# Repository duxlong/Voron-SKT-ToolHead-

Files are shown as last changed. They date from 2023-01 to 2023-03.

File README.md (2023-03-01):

# Voron SKT Toolhead
Mod for Voron with umbilical 
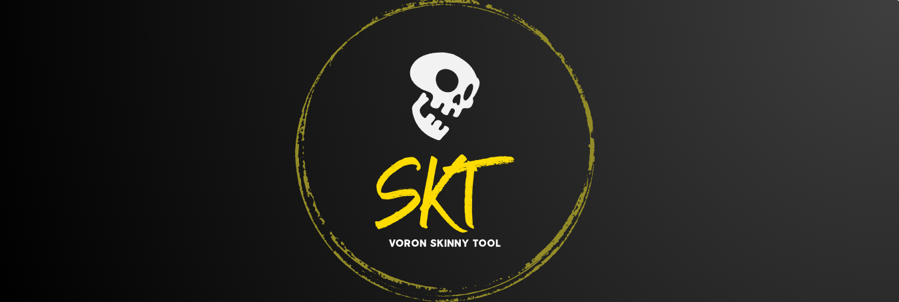
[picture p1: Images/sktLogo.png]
<br/>
<br/>
SKT stands for "Skinny Tool" :)<br/>
Some things are inspired by EVA 2, thanks guys.<br/>
This toolhead is designed to be as light as possible. It will not be compatible with all extruders and all hotends or even with all types of toolboards due to its design and specificity.<br/>
STK toolhead allow the installation of SHT42/EBB42 toolboards only.><br/>
If you want to run fast, just try it.<br/><br/>
There will be a CPAP cooling system as soon as possible (and will be compatible with Trident as well)<br/>

# Voron SKT Toolhead - Voron Tap Edition (for 2.4 and Trident)
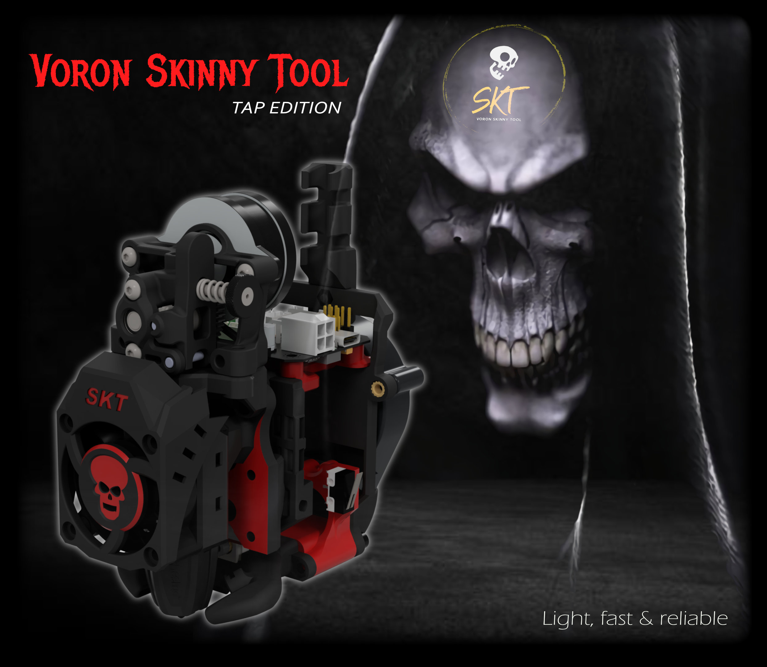
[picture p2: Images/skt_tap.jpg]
<br/>

# Voron SKT Toolhead - Klicky Edition (for 2.4, no Trident)
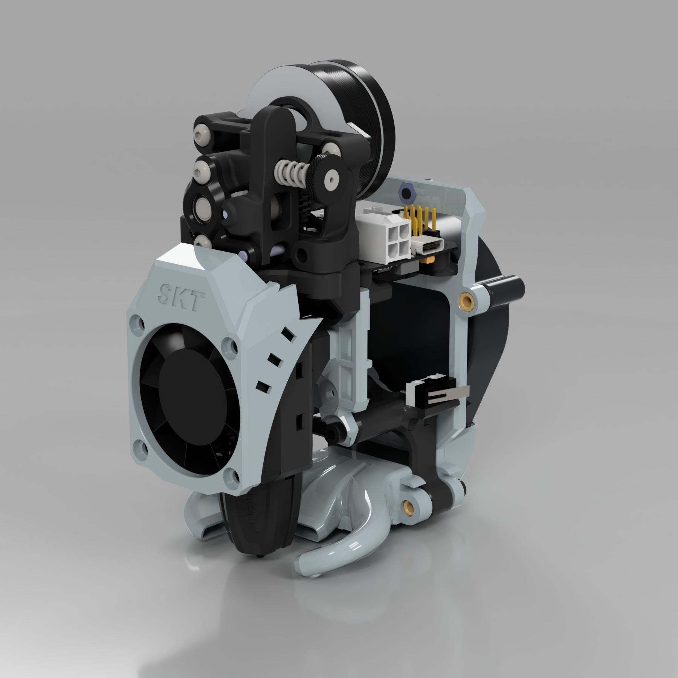
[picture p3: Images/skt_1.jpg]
<br/>
<br/>
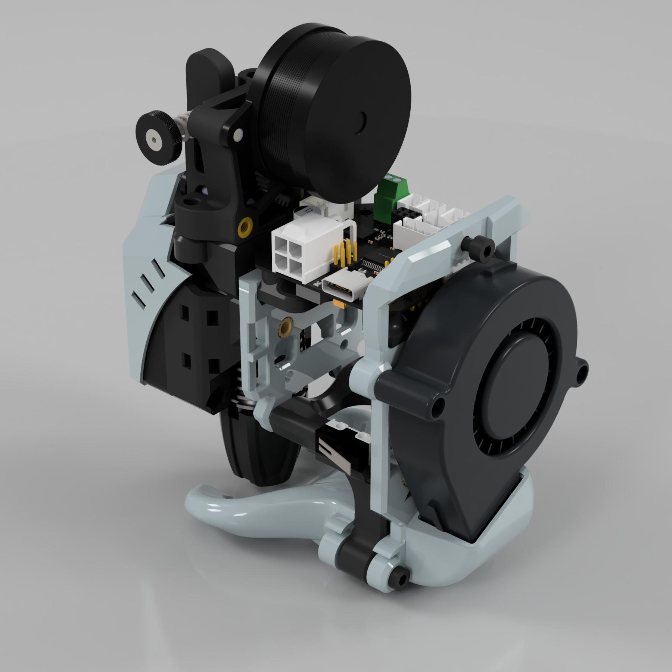
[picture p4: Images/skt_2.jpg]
<br/>
<br/>
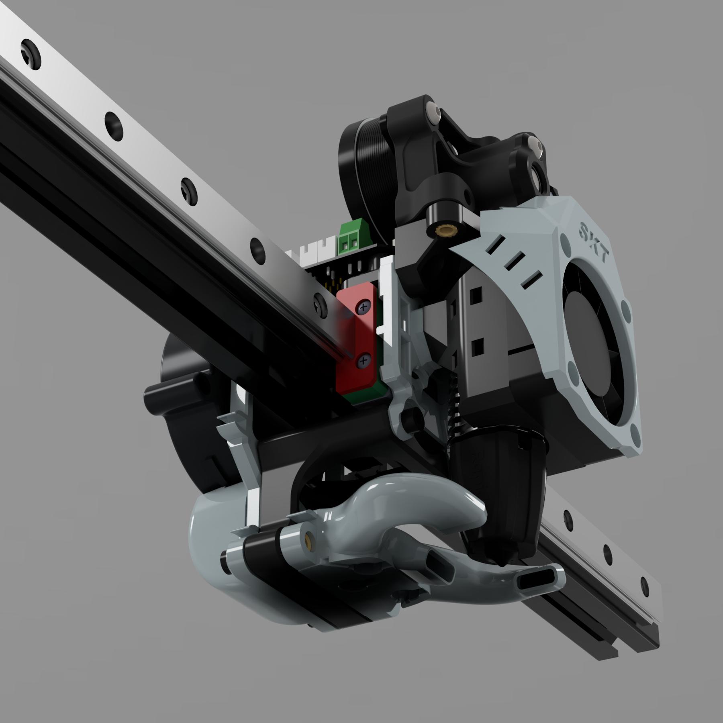
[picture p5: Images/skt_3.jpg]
<br/>

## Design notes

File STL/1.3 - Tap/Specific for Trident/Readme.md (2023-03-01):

ITA: Per installare l'SKT-TAP sulla trident è necessario stampare i pezzi presenti in questa cartella.

ENG: To install the SKT-TAP on the trident it is necessary to print the pieces present in this folder.

<i>Many thanks to Luca Lupi for the precious contribution</i>

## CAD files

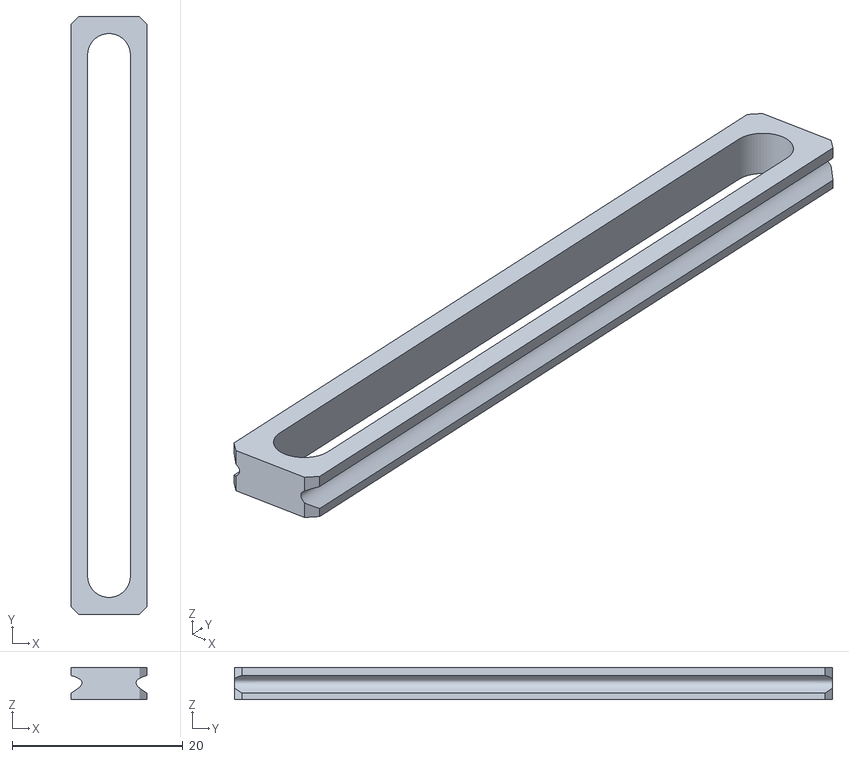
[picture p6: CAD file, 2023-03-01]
STL/1.3 - Tap/Tap System/MGN9_Assembly_Tool.stl
8.90 x 70.0 x 3.80

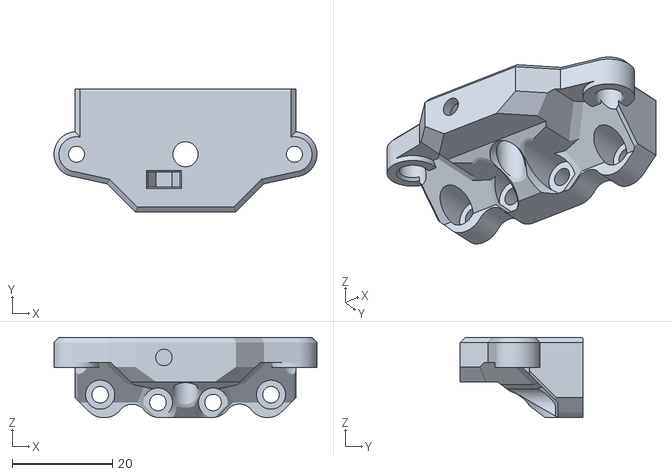
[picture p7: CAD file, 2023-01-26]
STL/1.2 - Klicky/Extruders/Supporto Sherpa Mini.stl
52.5 x 24.5 x 16.0

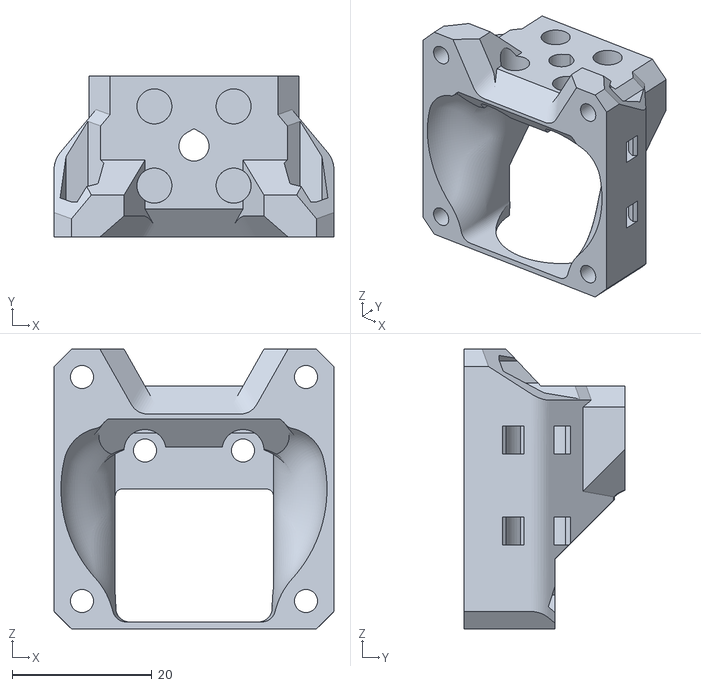
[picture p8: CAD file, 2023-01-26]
STL/1.2 - Klicky/Hotend/Masp MK8 HF/Supporto MASP MK8 HF.stl
40.0 x 23.0 x 40.0

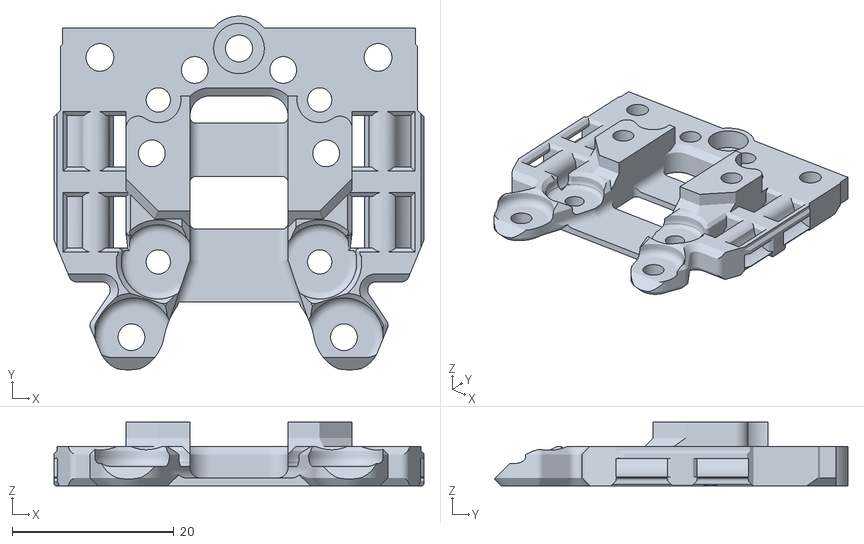
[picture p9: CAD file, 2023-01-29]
STL/1.2 - Klicky/Hotend/Rapido HF/Carrello - Parte anteriore.stl
45.7 x 43.7 x 7.90

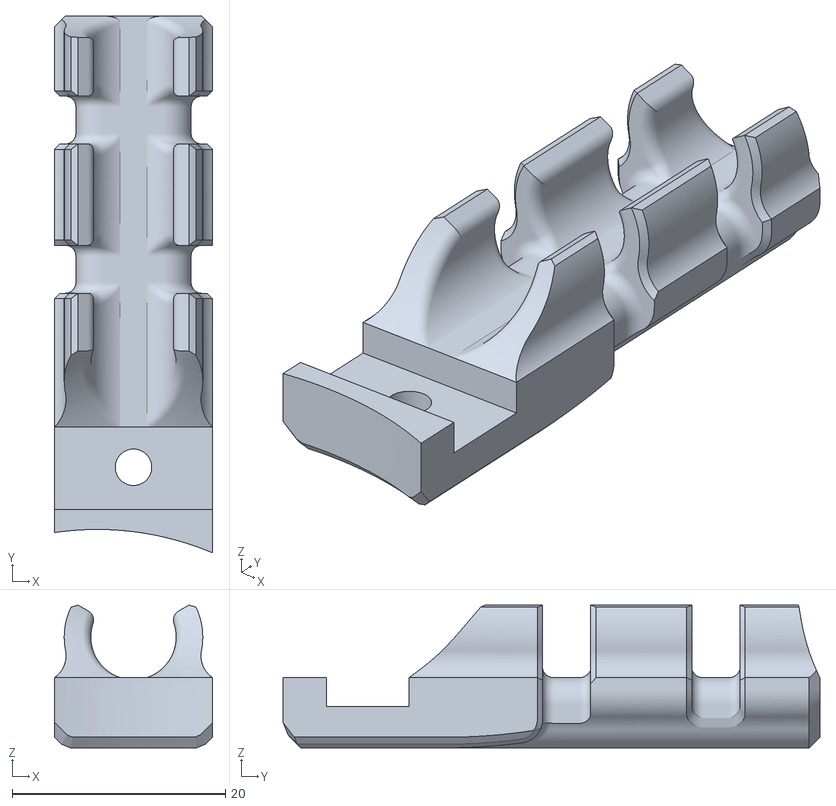
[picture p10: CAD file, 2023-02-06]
STL/1.2 - Klicky/Supporto ombelicale 8mm.stl
14.8 x 50.4 x 13.4

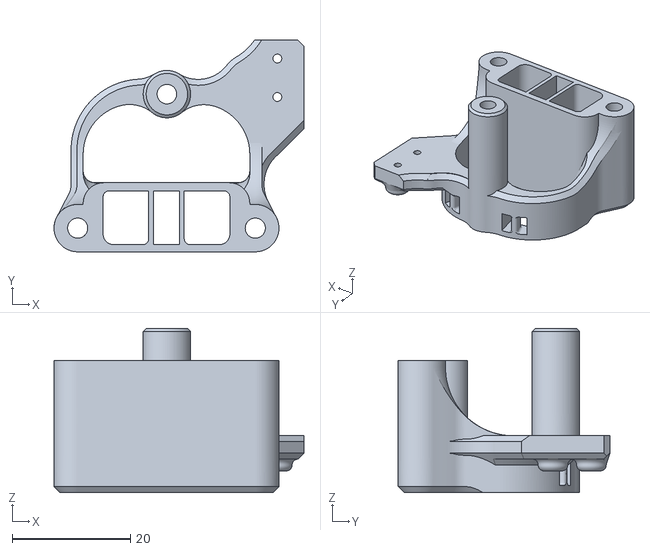
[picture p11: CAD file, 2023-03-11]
STL/1.3 - Tap/Carriage/Bottom.stl
42.2 x 35.7 x 27.7

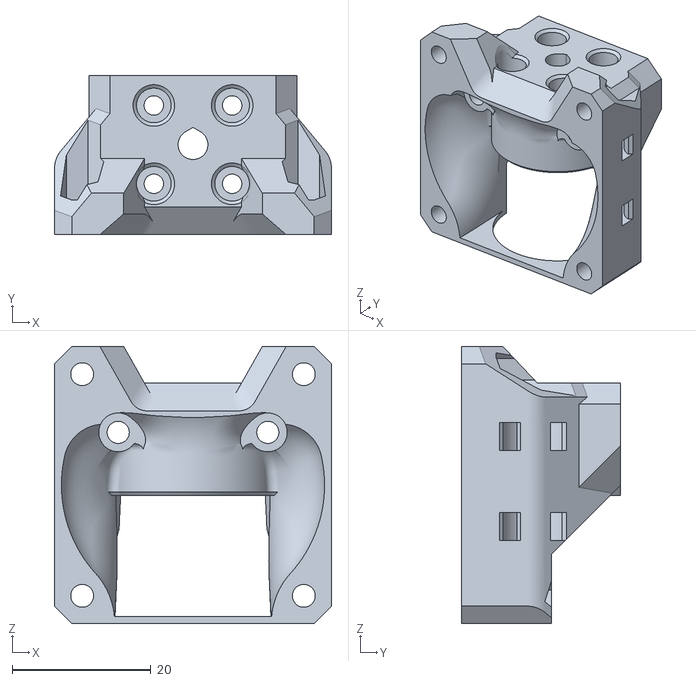
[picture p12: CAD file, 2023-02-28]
STL/1.3 - Tap/Hotend/Masp Drg HF/Mount for MASP DRG HF.stl
40.0 x 23.0 x 40.0

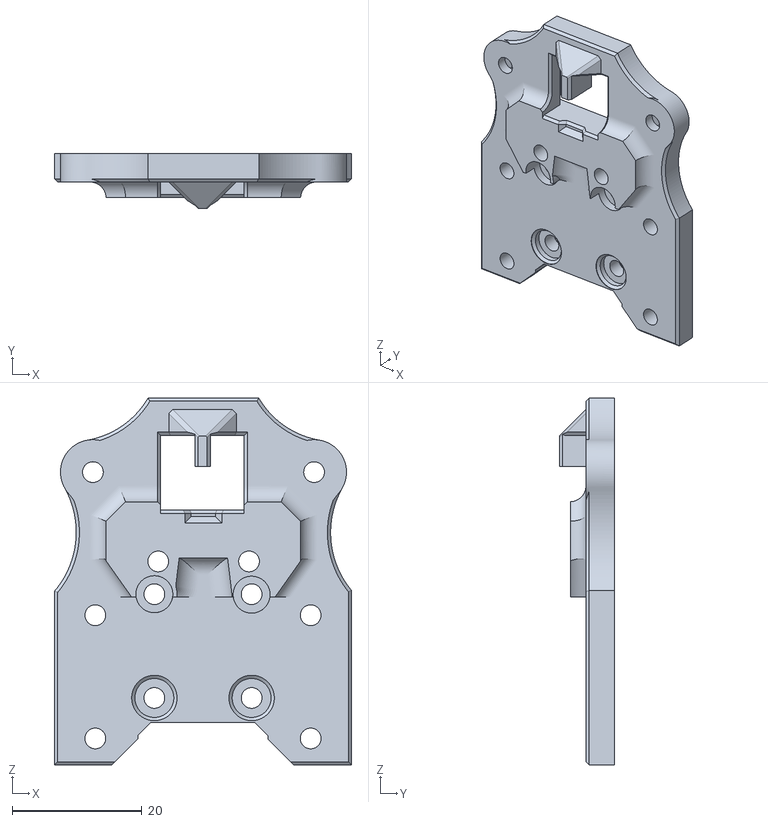
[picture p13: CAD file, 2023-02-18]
STL/1.3 - Tap/Hotend/Masp Mk8 HF/Front_Body_Tap.stl
45.8 x 8.49 x 56.6

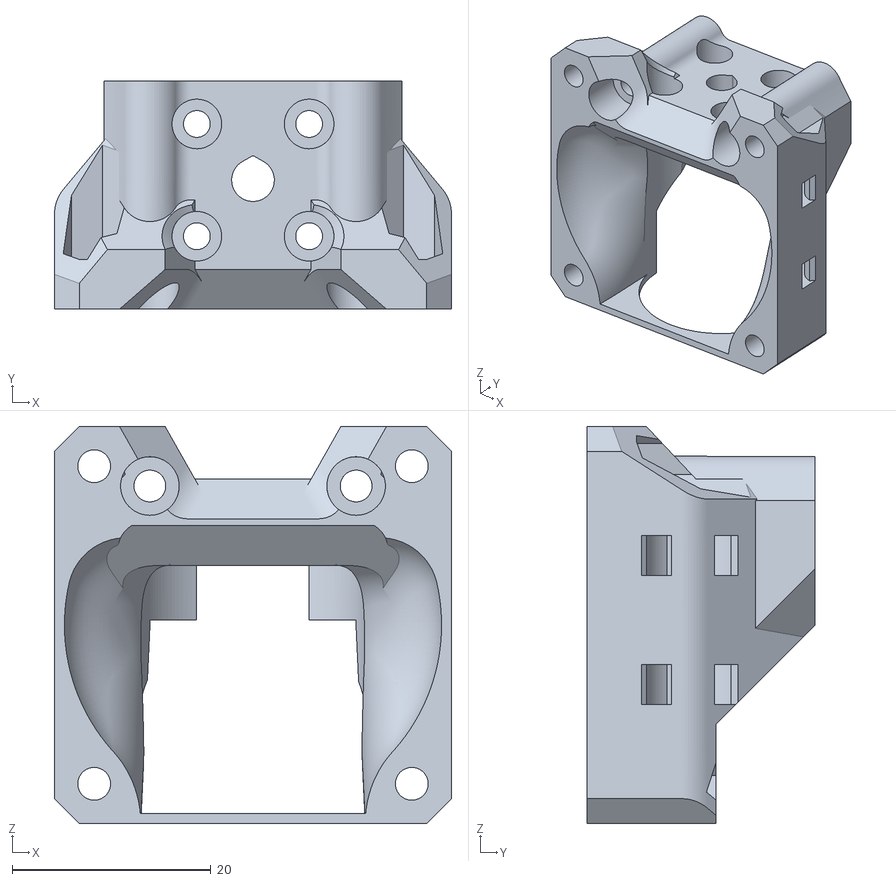
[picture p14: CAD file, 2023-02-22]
STL/1.3 - Tap/Hotend/Phaetus Dragon HF/Mount for Dragon HF.stl
40.0 x 23.0 x 40.0

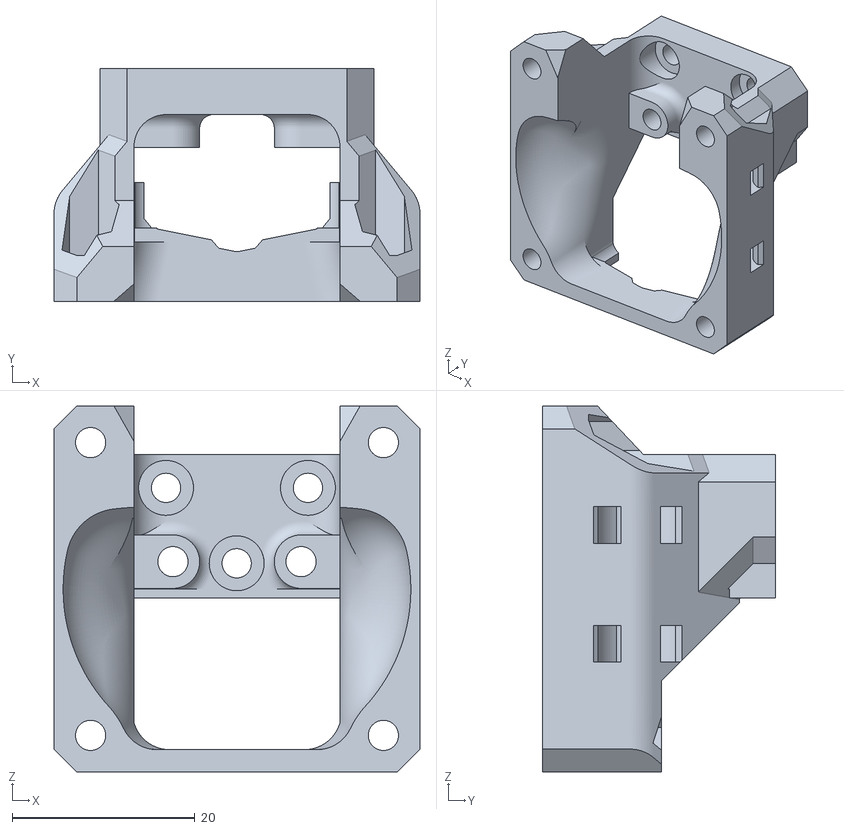
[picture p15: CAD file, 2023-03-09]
STL/1.3 - Tap/Hotend/Phaetus Taichi/Mount for Taichi.stl
40.0 x 25.4 x 40.0

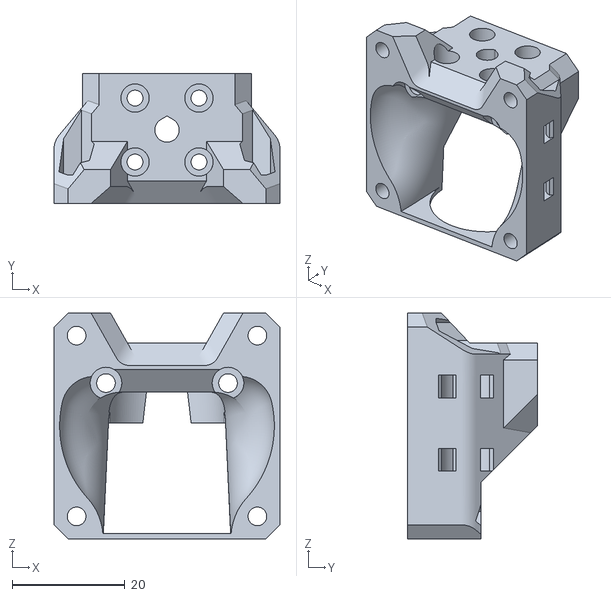
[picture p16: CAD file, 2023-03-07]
STL/1.3 - Tap/Hotend/Rapido HF/Mount for Rapido HF.stl
40.0 x 23.0 x 40.0

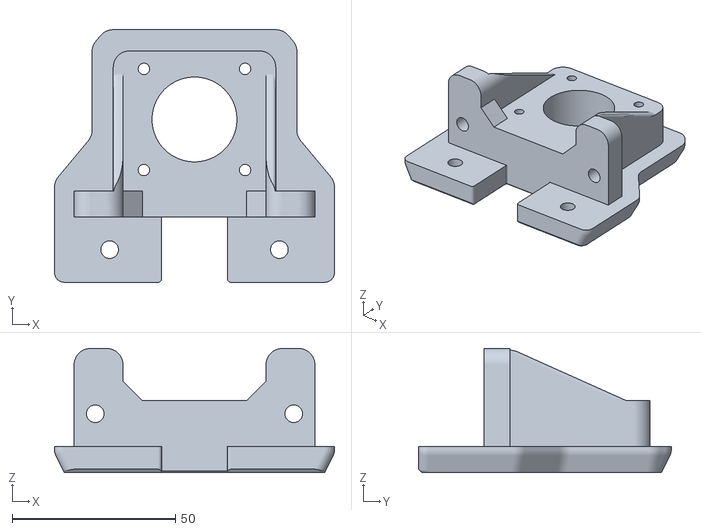
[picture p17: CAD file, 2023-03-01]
STL/1.3 - Tap/Specific for Trident/z_stepper_rear_skt-10mm.stl
85.8 x 77.4 x 38.0

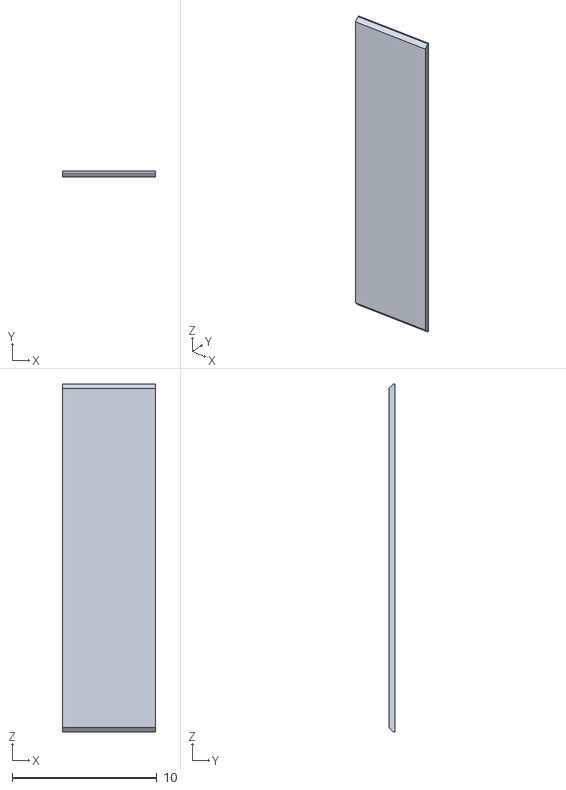
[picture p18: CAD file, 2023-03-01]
STL/1.3 - Tap/Tap System/Belt Spacers/Mgn12 Lektor Style - 0.4mm.stl
6.40 x 0.4 x 24.0

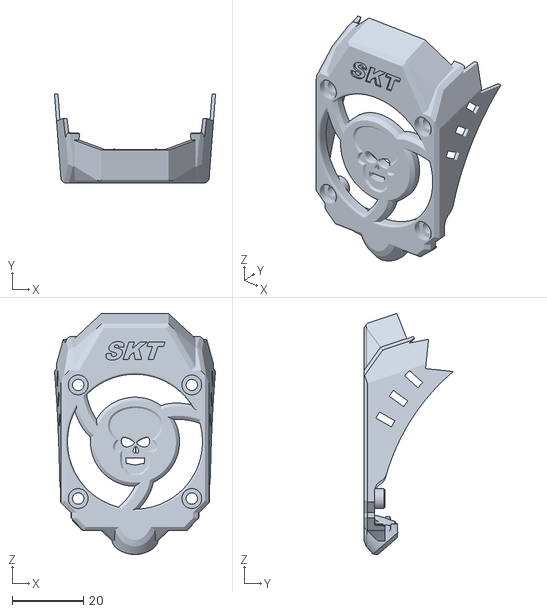
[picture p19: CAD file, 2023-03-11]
STL/FacePlates/Skull No Eyes - Neopixel.stl
45.4 x 25.2 x 67.9

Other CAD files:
STL/1.2 - Klicky/Carrello - Parte superiore - toolboard.stl
STL/1.2 - Klicky/Extruders/Supporto Vz-Hextrudort-High.stl
STL/1.2 - Klicky/Hotend/Masp MK8 HF/Carrello - Parte anteriore - MASP MK8 HF.stl
STL/1.2 - Klicky/Carrello - Parte Inferiore.stl
STL/1.2 - Klicky/Carrello - Parte posteriore.stl
STL/1.2 - Klicky/Dock Klicky SKT - 2.4 e Trident.stl
STL/1.2 - Klicky/Extruders/Supporto Sherpa Micro.stl
STL/1.2 - Klicky/Hotend/Rapido HF/Rapido mount.stl
STL/1.2 - Klicky/Probe Dock v2.stl
STL/1.3 - Tap/Carriage/Front.stl
STL/1.3 - Tap/Carriage/Rear.stl
STL/1.3 - Tap/Carriage/Top.stl
STL/1.3 - Tap/Extruders/Mount For Libra Mini.stl
STL/1.3 - Tap/Extruders/Mount for Lgx Lite.stl
STL/1.3 - Tap/Extruders/Mount for Orbiter 1.5.stl
STL/1.3 - Tap/Extruders/Mount for Sherpa Micro - No Front Screw.stl
STL/1.3 - Tap/Extruders/Mount for Sherpa Micro.stl
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

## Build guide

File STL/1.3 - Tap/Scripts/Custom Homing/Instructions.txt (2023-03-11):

1) Include the "SKT-Homing.cfg" file in the printer.cfg or copy its contents into your macro file if you have one.

2) In the printer.cfg file set [safe_z_home] as follows (or add it if not present):

[safe_z_home]
home_xy_position:117.5,117.5  #set your right coordinates of the center
speed:150				#set your preferred homing speed
z_hop:0				#Keep this value = 0

3) In the printer.cfg file add as follows:

[force_move]
enable_force_move: True		#Keep this value = True

4) In your macro of "END_PRINT" (it could be called something else) verify that there is "G28 X Y", if so add after the head has moved away from the bed

5) In your "PAUSE" macro set the parking coordinates as follows:

  {% set x_park = printer.toolhead.axis_maximum.x|float - 80.0  %}
  {% set y_park = printer.toolhead.axis_maximum.y|float - 40.0 %}

-end-

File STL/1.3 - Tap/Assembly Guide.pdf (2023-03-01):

# SKT

# TAP Edition

# ASSEMBLY GUIDE

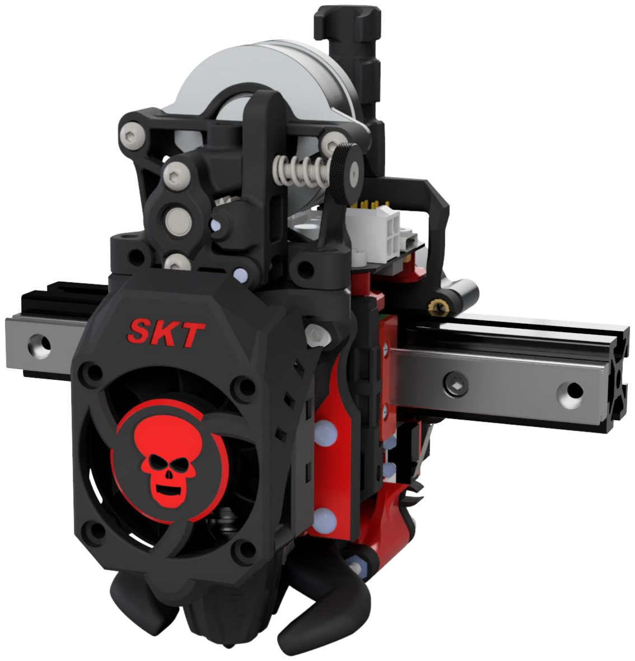
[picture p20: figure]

## Index

## Hardware reference

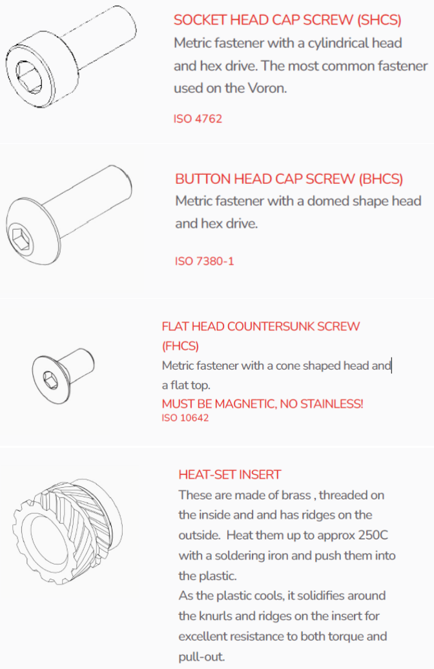
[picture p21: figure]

Threaded inserts have to be M3x5x4 type

## Step 1: Front carriage

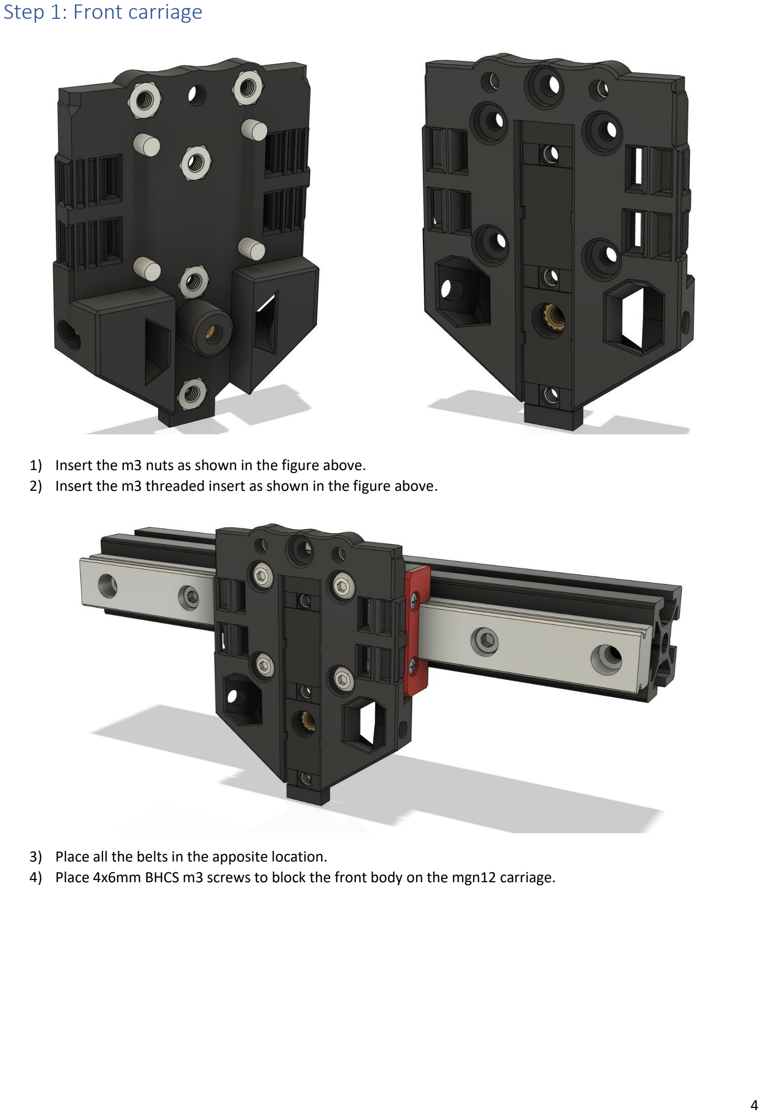
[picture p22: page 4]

1) Insert the m3 nuts as shown in the figure above.
2) Insert the m3 threaded insert as shown in the figure above.
3) Place all the belts in the apposite location.
4) Place 4x6mm BHCS m3 screws to block the front body on the mgn12 carriage.

## Step 2: Rear carriage

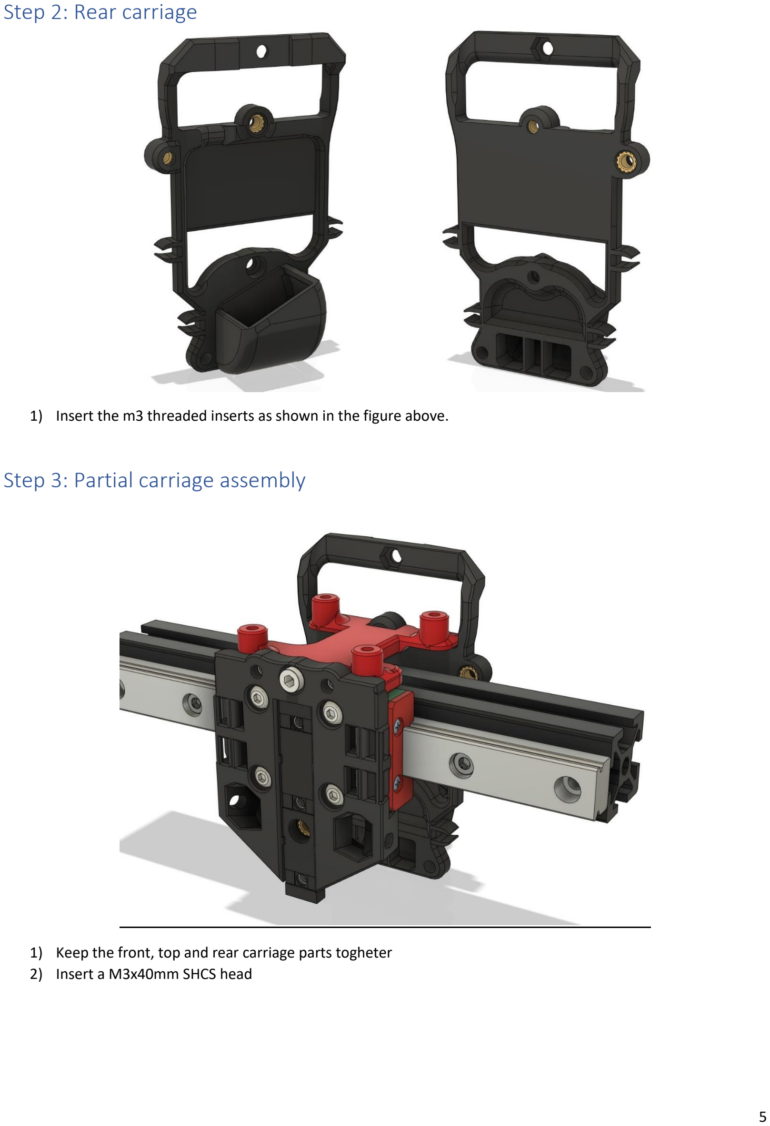
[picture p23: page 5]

1) Insert the m3 threaded inserts as shown in the figure above.

## Step 3: Partial carriage assembly

1) Keep the front, top and rear carriage parts togheter
2) Insert a M3x40mm SHCS head

## Step 4: Lower carriage assembly

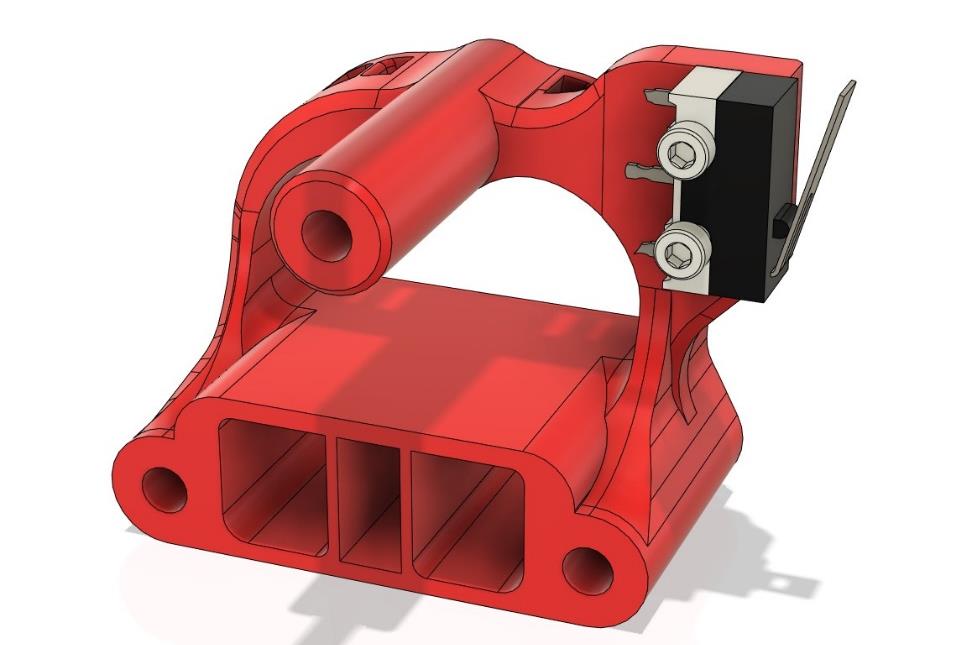
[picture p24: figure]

1) Insert 2 self-tapping screws M2x8mm (10mm as well) to lock the switch in right position

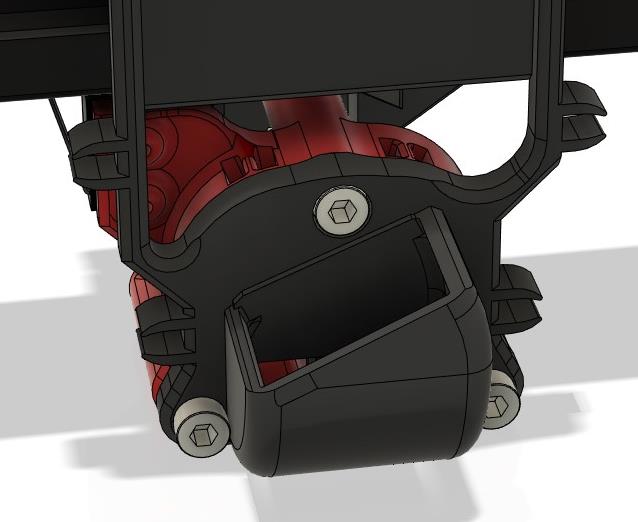
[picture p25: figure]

2) Insert 3 M3x35mm SHCS head as shown in the figure above. The center screw must be screwed into the front carriage insert.

## Step 5: Fanduct

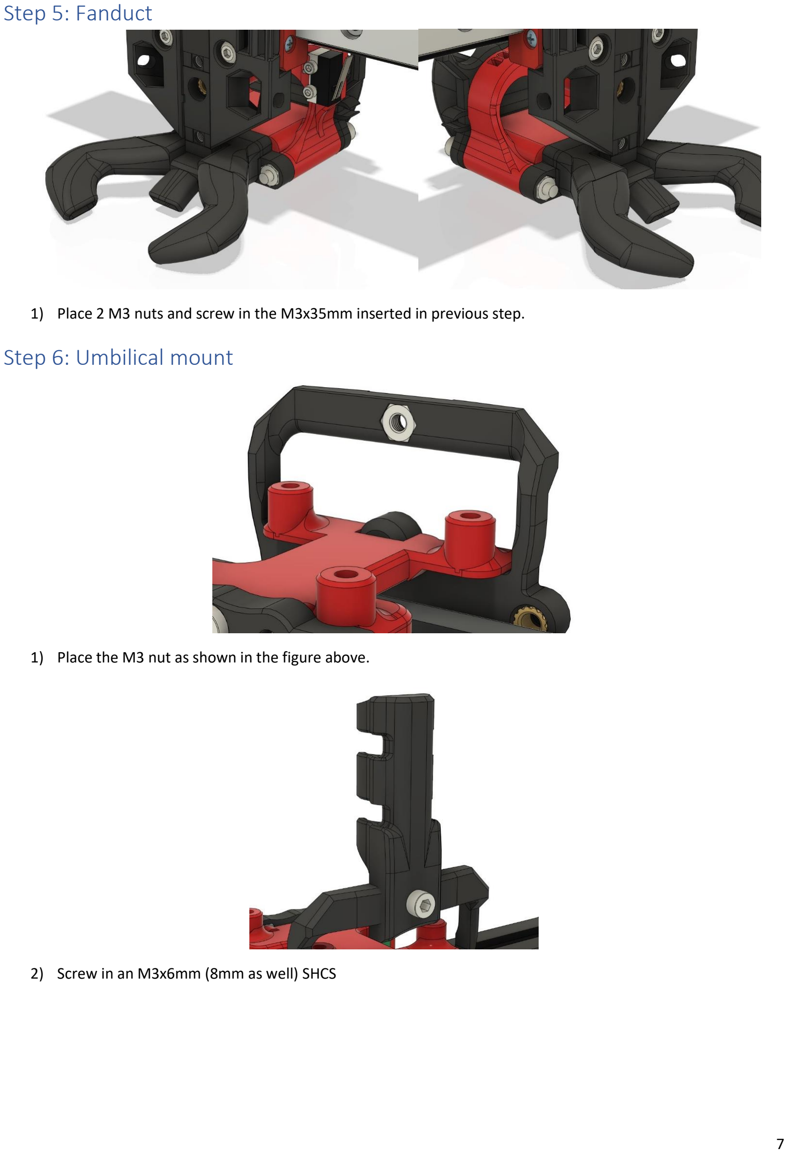
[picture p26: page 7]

1) Place 2 M3 nuts and screw in the M3x35mm inserted in previous step.

## Step 6: Umbilical mount

1) Place the M3 nut as shown in the figure above.
2) Screw in an M3x6mm (8mm as well) SHCS

## Step 7: Rear TAP system – initial assembly

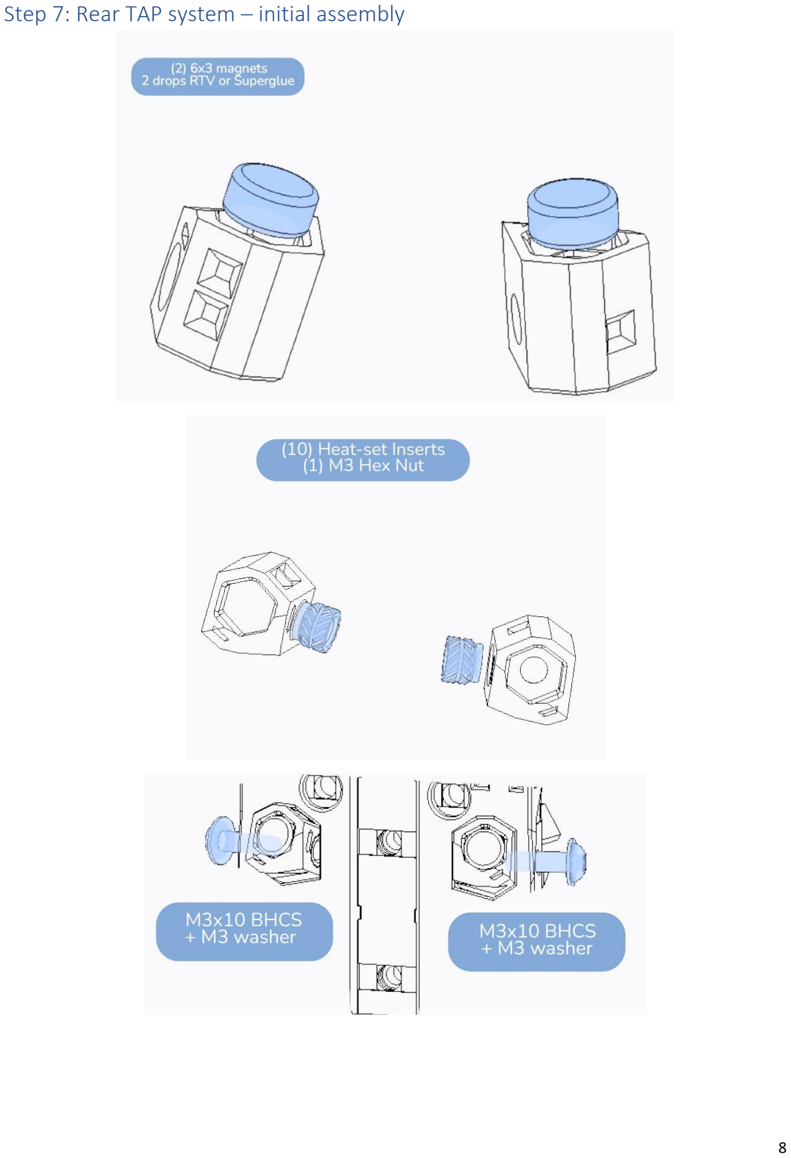
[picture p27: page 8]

## Step 8: Rear TAP system – MGN9 rail installation

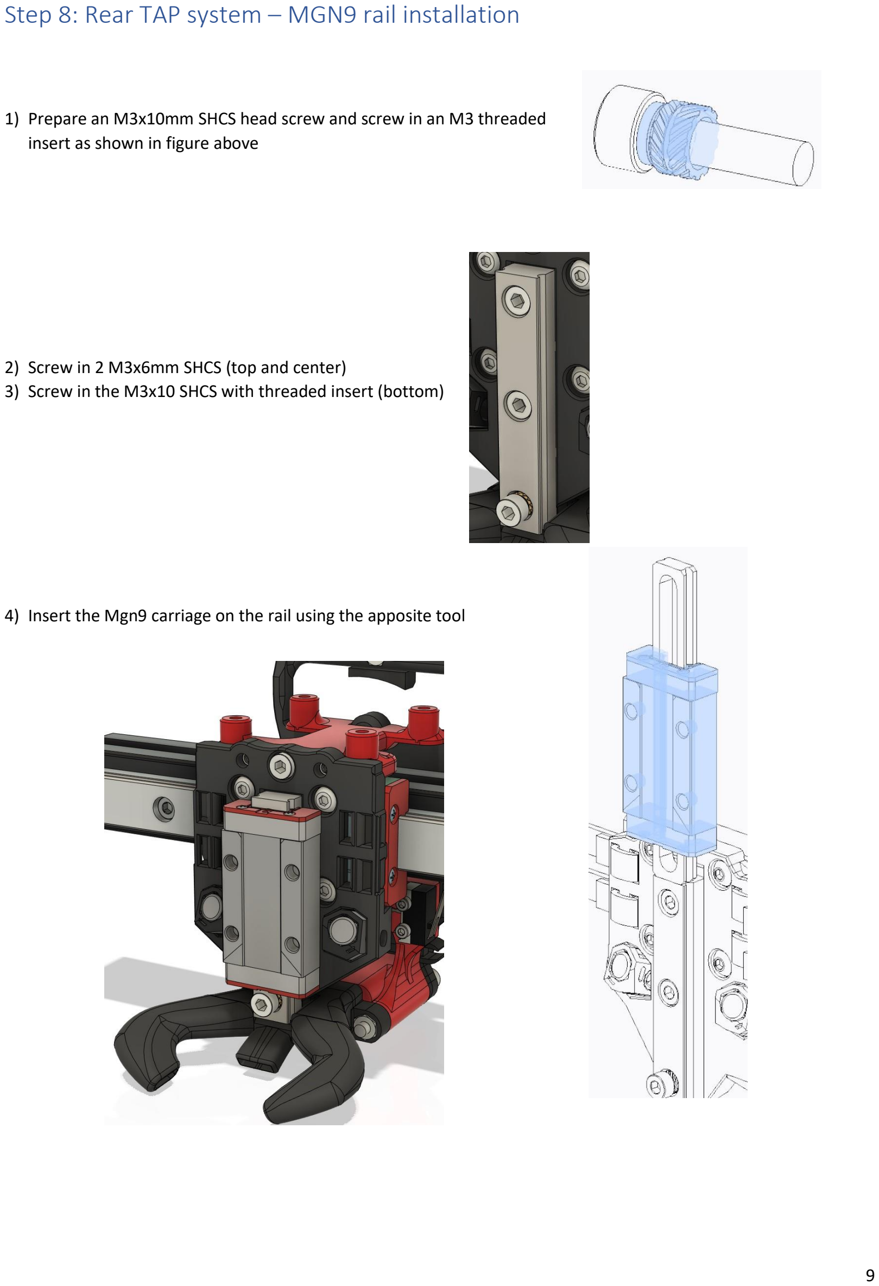
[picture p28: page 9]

1) Prepare an M3x10mm SHCS head screw and screw in an M3 threaded insert as shown in figure above
2) Screw in 2 M3x6mm SHCS (top and center)
3) Screw in the M3x10 SHCS with threaded insert (bottom)
4) Insert the Mgn9 carriage on the rail using the apposite tool

## Step 9: Rear TAP system – Probe installation

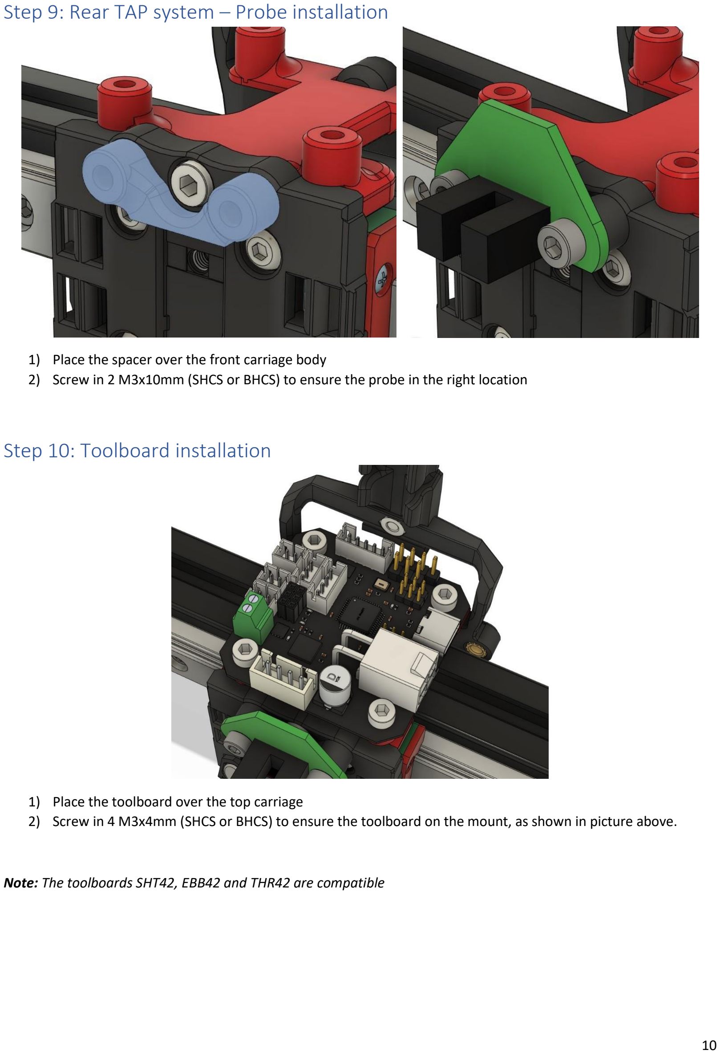
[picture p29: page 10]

1) Place the spacer over the front carriage body
2) Screw in 2 M3x10mm (SHCS or BHCS) to ensure the probe in the right location

## Step 10: Toolboard installation

1) Place the toolboard over the top carriage
2) Screw in 4 M3x4mm (SHCS or BHCS) to ensure the toolboard on the mount, as shown in picture above.

Note: The toolboards SHT42, EBB42 and THR42 are compatible

## Step 11: Front TAP system

1) Place 6 M3 nuts as shown in picture on the side

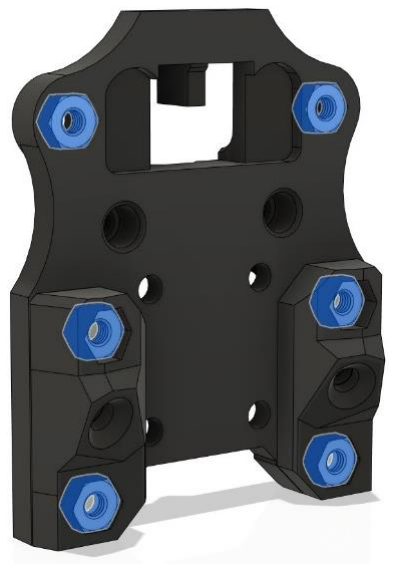
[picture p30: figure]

2) Screw in 4 M3x8mm BHCS as shown in picture on the side

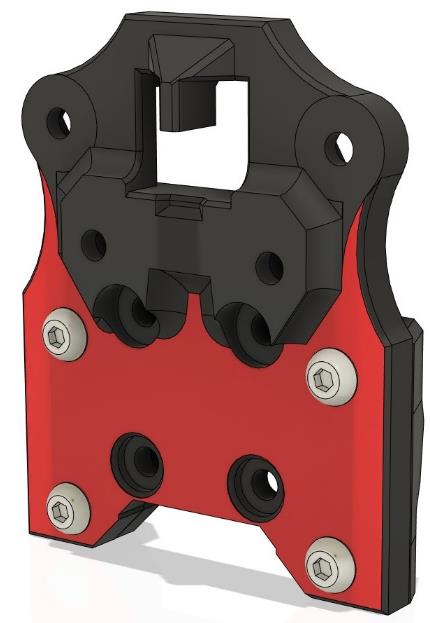
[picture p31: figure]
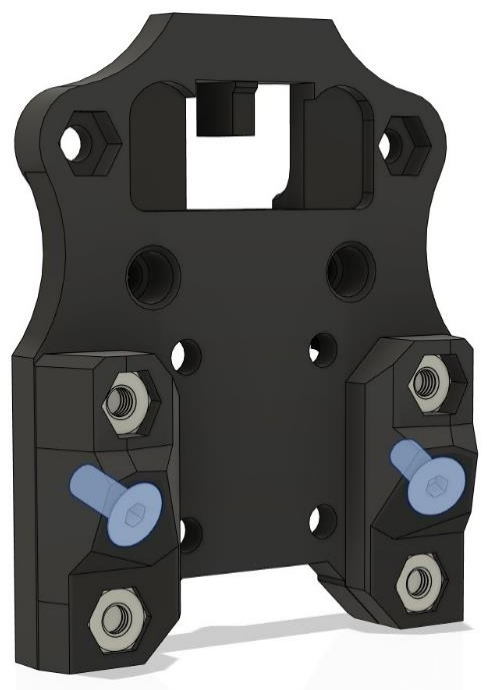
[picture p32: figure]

3) Screw in 2 M3x6mm FHCS as shown in picture on the side

The holes here are designed at an angle.
Go slow. Tighten the FHCS until they are flush, but do not over tighten.

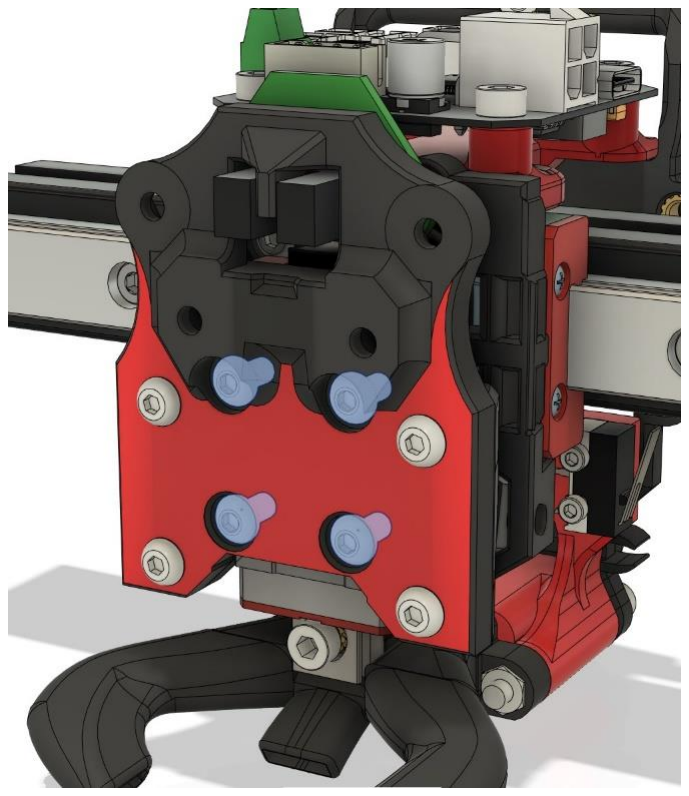
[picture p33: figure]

4) Screw in 4 M3x6mm BHCS as shown in picture on the side, to ensure the front tap system to the MGN9 carriage

## Step 12: Extruder adapter installation

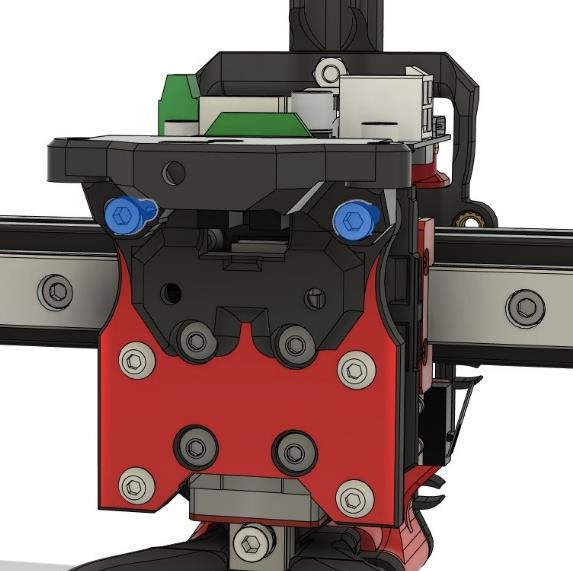
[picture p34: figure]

1) Place the adapter as show in side picture
2) Screw in 2 M3x8mm SHCS to ensure the adapter

## Step 12: Hotend installation

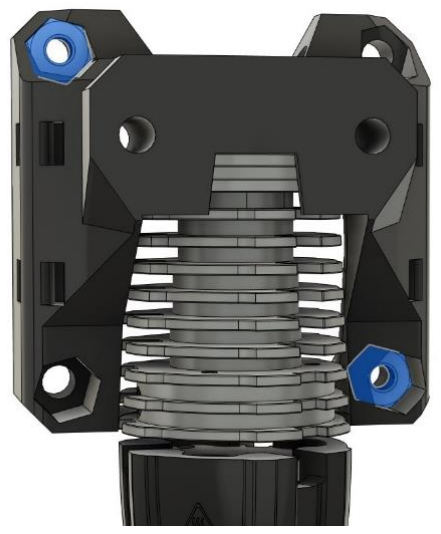
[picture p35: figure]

1) Insert 2 (4 if you want) M3 nuts as shown in side picture
2) Screw in 2 SHCS screws to ensure the hotend mount.

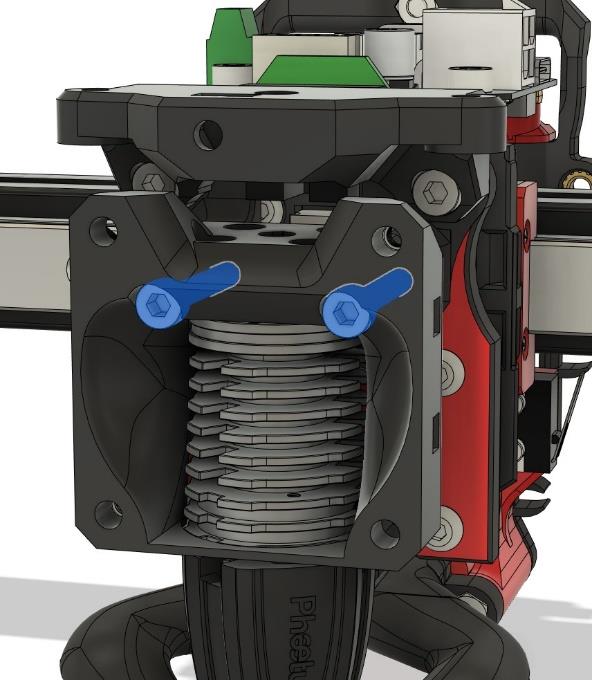
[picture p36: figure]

Note: The screws to be used in this step can change according to the different hotend types

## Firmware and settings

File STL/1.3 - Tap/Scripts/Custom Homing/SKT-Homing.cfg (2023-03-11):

[gcode_macro G28]
rename_existing: G28.1
gcode:

    {% set SafeXforHomingY = 80|float %}
    {% set SafeYforHomingY = 40|float %}
    {% set X = 0 %}
    {% set Y = 0 %}
    {% set Z = 0 %}

    {% if params.X is defined %}
      {% set X = 1 %}
    {% endif %}

    {% if params.Y is defined %}
      {% set Y = 1 %}
    {% endif %}
    
    {% if params.Z is defined %}
      {% set Z = 1 %}
    {% endif %}

    {action_respond_info("Homing: X:%s  Y:%s  Z:%s" % (X,Y,Z)) }
    {action_respond_info("Axis already homed: %s" % (printer.toolhead.homed_axes)) }
 
    #HOME DI X
    {% if X == 1 %}
     # {% if "y" not in printer.toolhead.homed_axes %} 
       # SET_KINEMATIC_POSITION Y=0 
       # G91
       # G0 Y{SafeYforHomingY}  F5000
       # G90
     # {% endif %}  
      {action_respond_info("Homing X")}
      G28.1 X
      G90
      G0 X{printer.toolhead.axis_maximum.x|float - SafeXforHomingY }  F5000      
    {% endif %}

    #HOME DI Y
    {% if Y == 1 %}
      {% if "x" not in printer.toolhead.homed_axes %} 
        G28.1 X
      {% else %}
        G90
        G0 X{printer.toolhead.axis_maximum.x|float - SafeXforHomingY }  F5000
      {% endif %}  
        {action_respond_info("Homing Y")}      
        G28.1 Y
        G90
        G0 Y{printer.toolhead.axis_maximum.y|float - SafeYforHomingY }  F5000      
    {% endif %}
    
    #HOME DI Z
    {% if Z==1 %}
      {% if "x" not in printer.toolhead.homed_axes %} 
        G28.1 X
      {% endif %}
      {% if "y" not in printer.toolhead.homed_axes %} 
        G28.1 Y
      {% endif %}
      {action_respond_info("Homing Z")}
      {% if "z" not in printer.toolhead.homed_axes %} 
        SET_KINEMATIC_POSITION Z=0 
      {% endif %}
      G28.1 Z
      G1 Z10
    {% endif %}

    {% if X==0 and Y==0 and Z==0 %}
        {action_respond_info("Homing all")}
        {% if "z" not in printer.toolhead.homed_axes %} 
            SET_KINEMATIC_POSITION Z=0 
        {% endif %}
        G91
        G1 Z{printer.gcode_move.gcode_position.z+10} F1500
        G90
        G28.1 X
        G0 X{printer.toolhead.axis_maximum.x|float - SafeXforHomingY }  F5000    
        G28.1 Y        
        G28.1 Z # Home z, because detector is on the bed, not the nozzle 
        G1 Z10
    {% endif %}

 

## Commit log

2023-01-29 Update Carrello - Parte anteriore.stl
    [Carrello - Parte anteriore.stl]
2023-02-15 Create Fan Duct + Klicky + Led.stl
2023-02-18 Tap edition ready
    [Bottom.stl, Carrello - Parte Inferiore.stl, Carrello - Parte anteriore - MASP MK8 HF.stl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]
2023-02-19 Extruders added
    [Mount for Orbiter 1.5.stl, Mount for Sherpa Micro.stl, Mount for Vz-Hextrudort Motor high.stl]
2023-02-20 Create Mount For Libra Mini.stl
    [Mount For Libra Mini.stl]
2023-02-21 Update FanDuct + led.stl
2023-02-22 Dragon hf update
    [Front_Body_tap.stl, Mount for Dragon HF.stl]
2023-02-25 Create Mount for Sherpa Micro - No Front Screw.stl
    [Mount for Sherpa Micro - No Front Screw.stl]
2023-02-27 add masp drg
    [Front_Body_tap.stl, Mount for MASP DRG HF.stl]
2023-02-28 Update Mount for MASP DRG HF.stl
    [Mount for MASP DRG HF.stl]
2023-03-01 trident update
    [z_stepper_rear_skt-10mm.stl]
2023-03-01 belt spacers added
    [Mgn12 Generic - 0.2mm.stl, Mgn12 Lektor Style - 0.4mm.stl]
2023-03-01 Create Assembly Guide.pdf
2023-03-01 Update Assembly Guide.pdf
2023-03-07 Update Mount for Rapido HF.stl
    [Mount for Rapido HF.stl]
2023-03-09 taichi added
    [Front_Body_Tap.stl, Mount for Taichi.stl]
2023-03-11 faceplate neopixel
    [Skull - Neopixel.stl, Skull No Eyes - Neopixel.stl]
2023-03-11 homing macro
    [SKT-Homing.cfg]
